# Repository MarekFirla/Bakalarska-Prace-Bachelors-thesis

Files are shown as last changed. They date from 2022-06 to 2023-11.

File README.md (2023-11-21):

# Bakalářská práce
BAKALÁŘSKÁ PRÁCE - KONSTRUKCE LINEÁRNÍCH HODIN

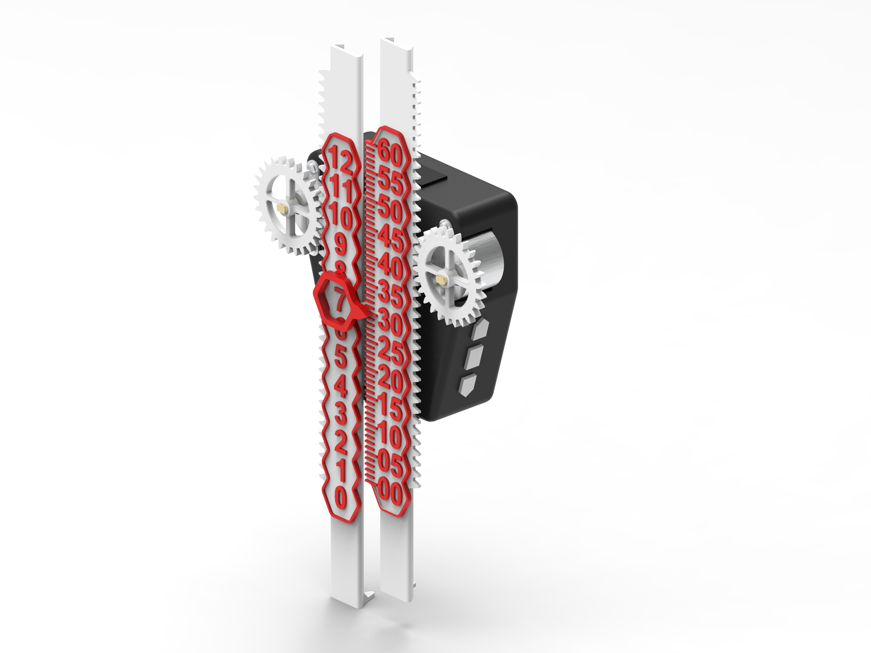
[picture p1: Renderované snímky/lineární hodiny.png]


Zadání bakalářské práce  

Ústav: Ústav konstruování  
Student: Marek Firla  
Studijní program: Strojírenství  
Studijní obor: Základy strojního inženýrství  
Vedoucí práce: doc. Ing. Petr Svoboda, Ph.D.  
Akademický rok: 2020/21  

Ředitel ústavu Vám v souladu se zákonem č.111/1998 o vysokých školách a se Studijním a zkušebním řádem VUT v Brně určuje následující téma bakalářské práce:  

Konstrukce lineárních hodin  
Stručná charakteristika problematiky úkolu:  
Zpravidla existují dvě široce využívaná rozhraní pro měření času. Na jedné straně analogové, které
k zobrazení času využívají rotující ručičky s číselníkem. Na druhé straně digitální s přímým výstupem
ukazatele času pomocí alfanumerických znaků na displeji. Za předpokladu, že čas plyne lineárně, je
však výzvou konstrukce lineárních hodin, které dokážou unikátní cestou zobrazit aktuální čas.

Typ práce: vývojová – konstrukční  

Cíle bakalářské práce:  
Hlavním cílem je konstrukce a následná realizace funkčního vzorku lineárních hodin užitím
technologie 3D tisku a řízené pomocí Arduino Uno s těmito parametry: stupnice s rozsahem 12 hodin
a rozlišitelností 5 minut.  

Dílčí cíle bakalářské práce:
– popsat současné konstrukce lineárních hodin,  
– definovat vhodné parametry pro konstrukční řešení,  
– navrhnout varianty konstrukčních uspořádání,  
– zpracovat výkresovou dokumentaci vybrané varianty včetně řídicího softwaru,  
– realizovat funkční vzorek pomocí 3D tisku.  

ABSTRAKT  
Cílem této práce je popsat návrh, konstrukci a výrobu lineárních hodin. V první části jsou popsány nynější řešení lineárních hodin. Druhá část popisuje návrh a výrobu prototypu lineárních hodin. Hodiny řídí mikrokontrolérová jednotka Arduino UNO, samotné měření času zprostředkovává modul reálného času a pohyb ukazatelů času zprostředkovává dvojice krokových motorů. Realizace je provedena pomocí 3D tisku.   

KLÍČOVÁ SLOVA   

Lineární hodiny, Arduino, 3D tisk  

ABSTRACT  
The main goal of this thesis is to describe the design, construction, and manufacture of linear clocks. The first part describes the current linear clocks design. The second part describes the design of a linear clock prototype. The linear clock is controlled by an Arduino UNO microcontroller unit, the time is measured by the real-time module, the movement of the time indicators is mediated by a pair of stepper motors. Manufacture is done using 3D printing.  

KEYWORDS  

Linear clock, Arduino, 3D print

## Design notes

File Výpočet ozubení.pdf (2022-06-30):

## PŘÍLOHA VÝPOČTY

## 1.1 Základní rozměry

Určení rozměrů základního profilu čelních ozubených kol s evolventním ozubením. Základní definice pojmů je uvedena v normě ČSN 01 4602. Význam jednotlivých pojmů lze

vidět na Obr. 1.

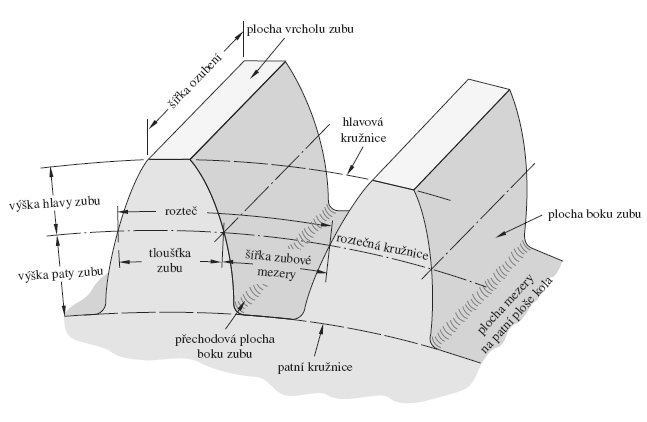
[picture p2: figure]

Obr. 1 Názvosloví čelního ozubeného [33]

### 1.1.1 Vstupní zvolené hodnoty:

Modul volen z tabulky normalizovaných modulů podle ČSN 01 4608:

mn = 1,5 mm

Úhel záběru volen podle ČSN 01 4607:

α = 20°

Jedná se o nekorigované ozubení, jednotkové posunutí je nulové:

x1 = 0

Úhel sklonu zubu je u přímého ozubení nulové:

β = 0°

Minimální počet zubů pastorku, který je v záběru s ozubeným hřebenem, aby nedocházelo k interferenci se určí z následující rovnice: [33], str. 729

zmin =

2 ∙ ℎa

∗
sin² α

=

2 ∙ 1
sin²(20°)

= 17,1 = 17̇

Zvolený počet zubů pastorku:

z1 = 26

Zvolená účinná šířka ozubení:

bw = 1,5 mm

### 1.1.2 Rozměry základního profilu ozubení

Rovnice pro výpočet rozměru ozubeného převodu převzato z [33], tab. 13-1 str. 741 (výběr z normy ČSN 01 4607).

Výška hlavy zubu:

ℎa = mn = 1,5 mm

Výška paty zubu:

ℎf = 1,25 ∙ mn = 1,25 ∙ 1,5 = 1,875 mm

Výška zubu:

ℎ = ℎa + ℎf = 1,5 + 1,875 = 3,375 mm

Hlavová vůle:

cn = 0,25 ∙ mn = 0,25 ∙ 1,5 = 0,375 mm

Rozteč:

pn = π ∙ mn = π ∙ 1,5 = 4,712 mm

Tloušťka zubu na roztečné kružnici:

sn = 0,5 ∙ pn = 0,5 ∙ 4,712 = 2,356 mm

Šířka zubové mezery:

en = sn = 2,356 mm

Poloměr zaoblení přechodové křivky:

pf = 0,38 ∙ mn = 0,38 ∙ 1,5 = 0,57 mm

Základní rozteč:

pb = pn ∙ cos(α) = 4,712 ∙ cos(20°) = 4,428 mm

### 1.1.3 Rozměry pastorku

Výpočet rozměrů přímých čelních ozubených kol [33], str. 722

Roztečná kružnice pastorku:

d1 = z1 ∙ mn = 26 ∙ 1,5 = 39 mm

Hlavová kružnice pastorku:

da1 = d1 + 2 ∙ ℎa = 39 + 2 ∙ 1,5 = 42 mm

Patní kružnice pastorku:

df1 = d1 − 2 ∙ ℎf = 39 − 2 ∙ 1,875 = 35,25 mm

Základní kružnice pastorku:

db1 = d1 ∙ cos(α) = 39 ∙ cos(20°) = 36,648 mm

Průměr valivé kružnice pastorku:

dw1 = d1 = 39 mm

### 1.1.4 Rozměry kola nahrazující hřeben

Pro pevnostní výpočty se ozubený hřeben nahradí ozubeným kolem o vysokém počtu zubů (1000 zubů) [22]

z2 = 1000

Roztečná kružnice kola:

d2 = z2 ∙ mn = 1000 ∙ 1,5 = 1 500 mm

Hlavová kružnice kola:

da2 = d2 + 2 ∙ ℎa = 1500 + 2 ∙ 1,5 = 1 503 mm

Patní kružnice kola:

df2 = d2 − 2 ∙ ℎf = 1500 − 2 ∙ 1,875 = 1 496,25 mm

Základní kružnice kola:

db2 = d2 ∙ cos(α) = 1500 ∙ cos(20°) = 1 409,54 mm

Průměr valivé kružnice kola:

dw2 = d2 = 1 500 mm

### 1.1.5 Součinitel záběru

Osová vzdálenost:

aw =

(z1+z2

)∙mn
2

=

(26+1000)∙1,5
2

= 769,50 mm

Součinitel záběru profilu v čelní rovině pro vnější ozubení [33], str. 727:

εα =

√da1
2 −db1

2 +√da2
2 −db2

2 −2∙aw∙sin(α)

2∙pb

=

√42²−36,648²+√1503²−1 409,54²−2∙769,50∙sin (20°)

2∙4,428

= 1,793

Součinitel záběru kroku:

εβ = 0

Celkový součinitel záběru:

εγ = εα + εβ = 1,793 + 0 = 1,793

## 1.2 Pevnostní výpočet

### 1.2.1 Zatížení

Určení zatížení ozubeného soukolí [33], str. 751

Jmenovitý kroutící moment krokového motoru určený z [15]:

M = 34,4 N ∙ mm

Obvodová síla kola:

Ft =

2M
d1

= 1,759 N

Radiální síla kola:

Fr = Ft

- tan(α) = 0,64 N

Normálná síla kola:

Fn =

Ft
cos (α)

= 1,872 N

### 1.2.2 Materiálové charakteristiky

Mez únavy v ohybu [25]:

σFP = 4,9 MPa

### 1.2.3 Kontrola na ohyb v patě zubu

Výpočet ohybového napětí v patě zubu bude vypočten dle ČSN 01 4686. Výpočet je

zjednodušený a platí pro čelní ozubená kola s přímým a šikmým ozubením. Výpočet se omezuje na ohybové namáhání v patě zubu. [24]

Součinitel tvaru zubu se odečte z přiloženého grafu viz Obr. 2 [24]

YF = 2,6

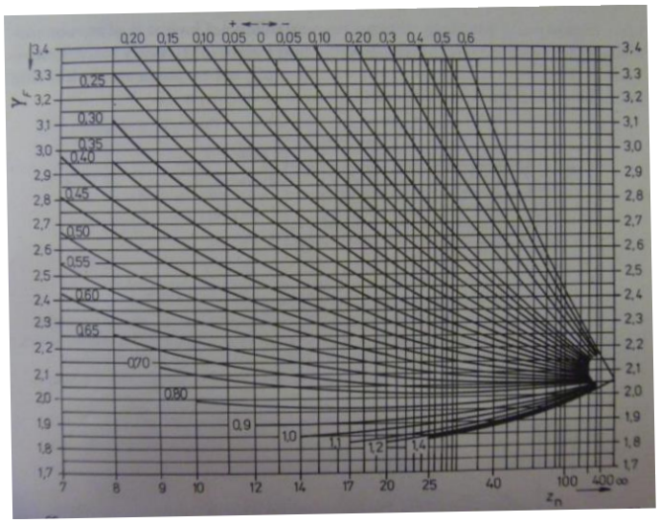
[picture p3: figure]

Obr. 2 Graf součinitele tvaru zubu [24]

Součinitel vlivu trvání záběru evolventy se spočítá z následující rovnice: [24]

Yε =

1
εα

=

1
1,793

= 0,558

Součinitel sklonu zubu se rovná pro přímé ozubení jedné:

Yβ = 1

Ohybové napětí v patě zubu: [24]

σF =

Ft
mn∙bw
- YF ∙ Yε
- Yβ =

1,759
1,5∙1,5
- 2,6 ∙ 0,558 ∙ 1 = 1,133 MPa

Bezpečnost:

SF =

σFP
σF

= 4,324

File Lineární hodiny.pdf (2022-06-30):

# VYSOKÉ UENÍ TECHNICKÉ V BRN

BRNO UNIVERSITY OF TECHNOLOGY

## FAKULTA STROJNÍHO INENÝRSTVÍ

FACULTY OF MECHANICAL ENGINEERING

## ÚSTAV KONSTRUOVÁNÍ

INSTITUTE OF MACHINE AND INDUSTRIAL DESIGN

# KONSTRUKCE LINEÁRNÍCH HODIN

DESIGN OF LINEAR CLOCK

### BAKALÁSKÁ PRÁCE

BACHELOR'S THESIS

### AUTOR PRÁCE

AUTHOR

### Marek Firla

### VEDOUCÍ PRÁCE

SUPERVISOR

doc. Ing. Petr Svoboda, Ph.D.

### BRNO 2021

Fakulta strojního inenýrství, Vysoké uení technické v Brn / Technická 2896/2 / 616 69 / Brno

# Zadání bakaláské práce

Ústav: | Ústav konstruování
Student: | Marek Firla
Studijní program: | Strojírenství
Studijní obor: | Základy strojního inenýrství
Vedoucí práce: | doc. Ing. Petr Svoboda, Ph.D.
Akademický rok: | 2020/21

editel ústavu Vám v souladu se zákonem .111/1998 o vysokých kolách a se Studijním a zkuebním ádem VUT v Brn uruje následující téma bakaláské práce:

## Konstrukce lineárních hodin

Struná charakteristika problematiky úkolu:
Zpravidla existují dv iroce vyuívaná rozhraní pro mení asu. Na jedné stran analogové, které k zobrazení asu vyuívají rotující ruiky s íselníkem. Na druhé stran digitální s pímým výstupem ukazatele asu pomocí alfanumerických znak na displeji. Za pedpokladu, e as plyne lineárn, je vak výzvou konstrukce lineárních hodin, které dokáou unikátní cestou zobrazit aktuální as.

Typ práce: vývojová konstrukní

Cíle bakaláské práce:
Hlavním cílem je konstrukce a následná realizace funkního vzorku lineárních hodin uitím technologie 3D tisku a ízené pomocí Arduino Uno s tmito parametry: stupnice s rozsahem 12 hodin a rozliitelností 5 minut.
Dílí cíle bakaláské práce:
popsat souasné konstrukce lineárních hodin,
definovat vhodné parametry pro konstrukní eení,
navrhnout varianty konstrukních uspoádání,
zpracovat výkresovou dokumentaci vybrané varianty vetn ídicího softwaru,
realizovat funkní vzorek pomocí 3D tisku.

Poadované výstupy: prvodní zpráva, výkresy souástí, výkres sestavení, digitální data. Rozsah práce: cca 27 000 znak (15 20 stran textu bez obrázk).
asový plán, struktura práce a ablona prvodní zprávy jsou závazné: http://ustavkonstruovani.cz/texty/bakalarskestudiumukonceni/

Fakulta strojního inenýrství, Vysoké uení technické v Brn / Technická 2896/2 / 616 69 / Brno

Seznam doporuené literatury:

BROWN, H. T. 507 Mechanical Movements: Mechanisms and Devices. 18th Edition. Wexford College Press, 2010. ISBN 978-1-60386-311-7.

MOLINE, D. J. WAGNER a E. VOLK. Model of a mechanical clock escapement. American Journal of Physics. 2012, 80(7), 599-606. DOI: 10.1119/1.4705517. ISSN 0002-9505.

MAJOR, F. G. Celestial and Mechanical Clocks. The Quantum Beat. New York, NY: Springer New York, 1998, 1-21. DOI: 10.1007/978-1-4757-2923-8_1. ISBN 978-1-4757-2925-2.

RAWLINGS, A. L. The Science of Clocks and Watches. 3rd. Upton, England: British Horological Society, 1993. ISBN 978-0-95096-213-9.

Termín odevzdání bakaláské práce je stanoven asovým plánem akademického roku 2020/21

V Brn, dne

L. S.

prof. Ing. Martin Hartl, Ph.D. editel ústavu

doc. Ing. Jaroslav Katolický, Ph.D. dkan fakulty

## ABSTRAKT

Cílem této práce je popsat návrh, konstrukci a výrobu lineárních hodin. V první části jsou popsány nynější řešení lineárních hodin. Druhá část popisuje návrh a výrobu prototypu lineárních hodin. Hodiny řídí mikrokontrolérová jednotka Arduino UNO, samotné měření času zprostředkovává modul reálného času a pohyb ukazatelů času zprostředkovává dvojice krokových motorů. Realizace je provedena pomocí 3D tisku.

## KLÍČOVÁ SLOVA

Lineární hodiny, Arduino, 3D tisk

## ABSTRACT

The main goal of this thesis is to describe the design, construction, and manufacture of linear clocks. The first part describes the current linear clocks design. The second part describes the design of a linear clock prototype. The linear clock is controlled by an Arduino UNO microcontroller unit, the time is measured by the real-time module, the movement of the time indicators is mediated by a pair of stepper motors. Manufacture is done using 3D printing.

## EYWORDS

Linear clock, Arduino, 3D print

## BIBLIOGRAFICKÁ CITACE

FIRLA, Marek. Konstrukce lineárních hodin. Brno, 2018, 99 s. Vysoké učení technické v Brně, Fakulta strojního inženýrství, Ústav konstruování. Vedoucí diplomové práce

doc. Ing. Petr Svoboda, Ph.D.

## PODĚKOVÁNÍ

Na tomto místě bych rád poděkoval doc. Ing. Petru Svobodovi, Ph.D. za odborné vedení mé práce.

## PROHLÁŠENÍ AUTORA O PŮVODNOSTI PRÁCE

Prohlašuji, že diplomovou práci jsem vypracoval samostatně, pod odborným vedením doc. Ing. Petra Svobody, Ph.D. Současně prohlašuji, že všechny zdroje obrazových a textových informací, ze kterých jsem čerpal, jsou řádně citovány v seznamu použitých zdrojů.

Podpis autora

## OBSAH

1 | ÚVOD | 13
2 | PŘEHLED SOUČASNÉHO STAVU POZNÁNÍ | 14
2.1 | Čas | 14
2.2 | Lineární hodiny | 14
| CLOQ The linear clock. | 16
| Linear Clockworks | 16
| Linear clock by JanDerogee | 17
| Linear clock by Euphy | 18
| Linear clock by Audun Ask Blaker | 18
2.3 | Arduino | 19
| Arduino IDE | 19
| Arduino UNO | 20
| Arduino klony | 20
| Arduino Shieldy | 20
3 | ANALÝZA PROBLÉMU A CÍL PRÁCE | 21
3.1 | Analýza problému | 21
3.2 | Cíl práce | 21
4 | KONCEPČNÍ ŘEŠENÍ | 22
4.1 | Komponenty | 22
| Řízení Hodin | 22
| Motory | 23
| Řízení motorů | 24
| Měření času | 24
| Ovládací rozhraní | 25
| Polohování | 25
4.2 | Koncepční uspořádání č. 1 | 26
4.3 | Koncepční uspořádání č. 2 | 27
4.4 | Koncepční uspořádání č. 3 | 27
5 | KONSTRUKČNÍ ŘEŠENÍ | 28
5.1 | Zapojení | 28
5.2 | Konstrukční rozvržení | 29

5.3 | Návrh krytů | 30
| Upevnění modulů | 30
5.4 | Převodový mechanismus | 32
| Převod ozubeným hřebenem | 32
| Vedení | 34
5.5 | Návrh ciferníků a indikátoru | 36
5.6 | Výroba | 36
| Materiál | 37
| Nastavení tisku | 37
5.7 | Sestavení programu | 38
| Načtení knihoven a deklarace proměnných | 39
| Nastavení zařízení | 40
| Hlavní struktura programu | 41
| Synchronizace | 42
| Nastavení výchozí polohy | 42
| Nastavení hodin | 43
| Alarm | 44
| Ošetření zákmitů tlačítek | 45
| Spotřeba energie | 45
5.8 | Sestavení lineárních hodin | 45
5.9 | Náklady | 47
6 | DISKUZE | 49
7 | ZÁVĚR | 50
8 | SEZNAM POUŽITÝCH ZDROJŮ | 51
9 | SEZNAM POUŽITÝCH ZKRATEK, SYMBOLŮ A VELIČIN | 54
10 | SEZNAM TABULEK | 56
11 | SEZNAM OBRÁZKŮ A GRAFŮ | 57
12 | SEZNAM PŘÍLOH | 58

## 1 ÚVOD

Čas je pro celé lidstvo klíčovým faktorem už od jeho počátku. Tento fakt přinesl vytvoření

nejen časových systémů, ale taktéž vývoj časomír. Vývoj probíhal nejen z hlediska stále přesnějšího měření času, ale také se měnily způsoby jeho zobrazení. Pokud se na současné časomíry podíváme v souvislosti s rozhraním pro zobrazovaní času tak narazíme na dvě nejvíce rozšířené varianty. První je analogové rozhraní zahrnující pevný ciferník a dvě nebo tři pohyblivé ručičky pro hodiny a minuty, popřípadě i sekundy. Druhou možností je zobrazení času skrze znaky na alfanumerickém displeji. Méně tradiční způsob zobrazení času nám poskytují lineární hodiny. Právě proto je poskytnutí rešerše dosavadních znalostí a návrh lineárních hodin cílem této bakalářské práce.

Jelikož trh s tímto řešením zobrazení času není příliš rozsáhlý, bylo nasnadě vytvořit nový konstrukčně jednoduchý funkční model levných lineárních hodin realizovaný pomocí 3D tisku a řízený skrze mikrokontrolérovou jednotku Arduino.

## 2 PŘEHLED SOUČASNÉHO STAVU POZNÁNÍ

## 2.1 Čas

Čas je základní fyzikální veličina soustavy SI s označením t. Může být definována jako:

Neprostorové kontinuum, ve kterém se události odehrávají ve zjevně nevratném pořadí od minulosti přes přítomnost až do budoucnosti. [1] Základní jednotkou je sekunda. Sekunda, značka „s“, je jednotka času v SI. Je definována fixací číselné hodnoty cesiové frekvence ΔνCs, tedy frekvence přechodu mezi hladinami velmi jemného rozštěpení neporušeného základního stavu atomu cesia 133, aby byla rovna 9 192 631 770, je-li vyjádřena jednotkou Hz, rovnou s−1. [2]

Hodiny (časomíry) jsou přístroje určené k přímému měření času. Měření času v nich probíhá z pravidla dvojím způsobem. Buď přímým sledováním rovnoměrného pohybu anebo počítáním pravidelných pohybů mechanických, elektrických nebo atomárních oscilací. [3] První způsob měření času je typický pro sluneční, přesýpací nebo vodní hodiny. Druhý způsob měření času je častější. Jedná o hodiny mechanické, kde se sleduje pohyb kyvadla, elektronické, využívající piezoelektrického jevu, nebo atomové kde se sleduje rezonanční frekvence atomu nejčastěji celsia.

## 2.2 Lineární hodiny

Lineární hodiny je časomíra s jedinečným způsobem zobrazení času, jejímž charakteristickým znakem je nahrazení tradičního kulatého ciferníku nebo alfanumerického displeje, ciferníkem přímým. Ručičky, ciferníky nebo jiné indikátory se pohybují po lineární, křivočaré, lomené nebo smíšené trajektorii a na následně se vracejí do výchozí polohy. [4] Jinými slovy indikátory se pohybují po neuzavřené křivce vratným pohybem.

Jeden z prvních konceptů lineárních hodin byl vytvořen kolem roku 1941. Nicméně původní zařízení sloužilo pouze pro zobrazování času jako dodatek ke standartnímu mechanickému hodinovému strojku. [4] Zařízení se připojovalo na příslušnou hodinovou minutovou nebo i sekundovou výstupní hřídel hodin.

Samotné zařízení se skládá z ciferníku ve tvaru lišty (viz Obr. 2-1 Koncepční náčrt řešení lineárních hodin) s čísly symbolizující hodiny. Na obou koncích ciferníku se nachází dvojice kladek (G, G´) na kterých je navinuto lanko (X), na němž je pevně ukotven indikátor času (R). Indikátor času (R) je uložen v lineárním vedení (V). První z kladek (G) je spojena s výstupní hřídelí hodinového strojku pomocí spojky. Spojka se skládá ze čtyř součástí: páky (CDE), drápu (A), tažné pružiny (J) a dorazu (K). Chodem hodinového strojku se otáčí i kladka (G) na kterou se navíjí lanko (X) a pohybuje se i indikátor (R) po ciferníku. Druhá kladka (G´) ze které se lanko (X) odvíjí, je spojena se spirálovou pružinou (P´). Otáčením kladky (G´), v důsledku odvíjení lana (X), se spirálová pružina (P´) stlačuje a vytváří kroutící moment (S´´), který působí proti pohybu. Jednou za celou otáčku kladky (G) se spojka (páka CDE a „dráp“ A) rozepne a rozpojí hodinový strojek od kladky (G), čímž se kladka (G) začne volně otáčet. Stlačená pružina (P´) poté začne otáčet kladkou (G´) a navíjet lanko (X), čímž se posune indikátor času (R) zpět do výchozí polohy. [4]

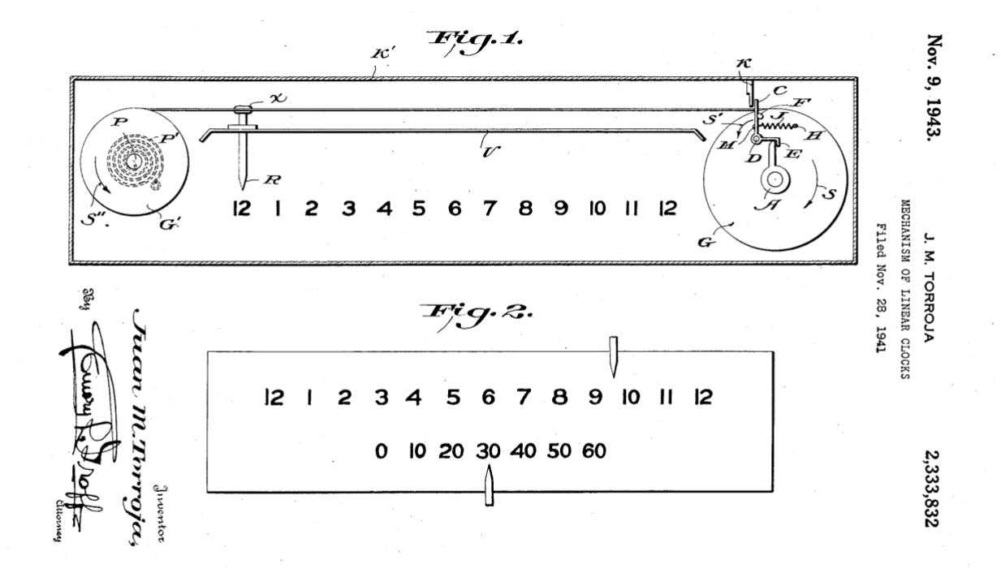
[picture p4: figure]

Obr. 2-1 Koncepční náčrt řešení lineárních hodin [4]

V současnosti se výrobou a prodejem tohoto netradičního způsobu zobrazování času zabývá jen velmi málo firem. Díky tomu mnoho návrhů na konstrukci pochází z dílny amatérů a hobby tvůrců. Projekty, z nichž jsem čerpal inspiraci pro vytvoření vlastního modelu, představím v následujících kapitolách.

CLOQ The linear clock.

Se zajímavým řešení lineárních hodin přišel britský designer Rob Lafratta (http://roblafratta.com/) v roce 2015. Jeho koncept lineárních hodin se inspiruje starými analogovými rádii a experimentuje s myšlenkou o zobrazení času v jedné linii. Jeho vize byla zjednodušit design standartních hodin s kruhovým ciferníkem a přinést zajímavé řešení zobrazení času. [5]

Samotné hodiny ovšem na rozdíl od původního konceptu neobsahují pohyblivé součásti a zobrazování hodin zde probíhá pomocí LED podsvícení. Každé z čísel na liště zde představuje příslušnou hodinu a podsvícením určitého čísla se určí aktuální hodina. Minuty jsou reprezentovány tečkami pod číslicemi hodin. Počet rozsvícených teček pak představuje pětiminutový časový interval.

Design hodiny si můžeme prohlédnout na přiloženém obrázku (viz Obr. 2-2)

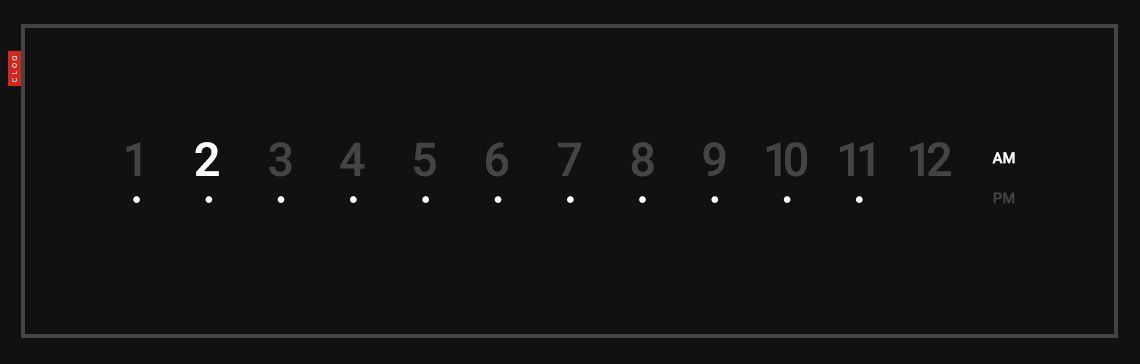
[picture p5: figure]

Obr. 2-2 Design CLOQ lineárních hodin [5]

### Linear Clockworks

Další řešení lineárních hodin přináší konstruktér Lindsay Morris a jeho firma Linear Clockworks (USA – Asheville), která vyrábí lineární hodiny na zakázku.

Samotné lineární hodiny se skládají z ciferníku, který je v podobě dlouhé lišty s čísly od 6 do 12 (viz obr. 2-3). Po tomto ciferníku se během dne směrem doprava pohybuje pouze jeden ukazatel, který určuje aktuální čas s rozlišitelností 15 minut. O půlnoci se pohyb reverzuje a ukazatel se začne pohybovat zpět doleva, přičemž návrat do výchozí polohy na 6:00 trvá šest hodin. Samotný ukazatel je pevně spojený s krytem pro elektroniku, která se pohybuje společně s ukazatelem. Řídící jednotka se skládá z řídícího obvodu, obvodu reálného času

(RTC obvod), displeje pro pohodlnější nastavení času a dvou tlačítek. Samotný pohyb potom zajišťuje připojený krokový motor. Hodiny jsou napájeny baterií, která vydrží 9 až 12 měsíců a dobíjí se pomocí USB konektoru. Firma vyrobené lineární hodiny prodává od 250 od 925 dolarů v závislosti na zvoleném designu. [6]

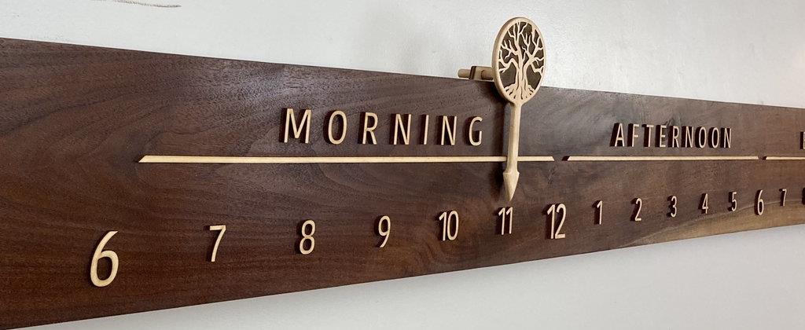
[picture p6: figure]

Obr. 2- 3 Jeden z designů nabízející firma Linear Clockworks [6]

### Linear clock by JanDerogee

Tyto lineární hodiny se inspirují designem starých mechanických hodin a uveřejnil je Jan Derogee na svých osobních webových stánkách.

Ciferník je rozdělen do dvou sloupců, ve kterých jsou napsány číslice symbolizující hodiny (viz obr. 2-4). Levý sloupec symbolizuje dopolední hodiny, pravý odpolední. Mezi sloupci se ve středu ciferníku nachází závitová tyč, na které se nachází jediná ručička. Samotná ručička je pak opřena o vodivou „senzorovou tyč“, umístěnou na vnějších stranách ciferníku, která slouží jako opora ručičky a taktéž se na ni nastavuje čas alarmu. V případě, že se závitová tyč otáčí, dochází k zvedání nebo spouštění ručičky, která určuje aktuální čas. Tato závitová tyč je pevně spojena s výstupní hřídelí krokového motoru. Motor se nachází ve spodní časti hodin společně s řídící elektronikou. Hodiny řídí mikročip ESP8266. Požitý krokový motor má označení 28BYJ-48. Na hodinách se taktéž nachází dvojice reproduktorů pro zvukovou signalizaci alarmu. [7]

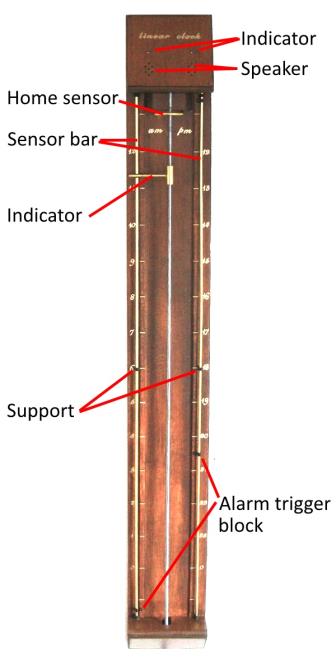
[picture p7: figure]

Obr. 2-4 Design lineárních hodin [7]

### Linear clock by Euphy

Tento projekt opět přinesl trochu odlišný přístup k řešení lineárních hodin, který více reflektuje původní koncept.

Základem je opět dlouhý ciferním ve tvaru lišty s čísly hodin a minut. Přímo na jednom z konců ciferníku jsou připevněny krokové motory a řídící elektronika jejichž hlavním kontrolérem je deska Arduino UNO. Na každé z výstupních hřídelí krokových motorů se nachází dva páry kladek. Další samostatná pomocná kladka je umístěna na opačném konci ciferníku. Na jednu z kladek na hřídeli motoru je namotáno lanko, které je následně přetaženo přes pomocnou kladku a upevněno k druhé kladce na hřídeli motoru. [8] Otáčením se převíjí lanko z jedné kladky na hřídeli motoru přes pomocnou kladku na kladku druhou. Na lanku je poté umístěn indikátor, který se přesouvá společně s ním po ciferníku čímž se zobrazuje čas.

### Linear clock by Audun Ask Blaker

Tyto lineární hodiny vytvořil průmyslový designér Audun Ask Blaker. (https://askblaker.com/)

Čas je zde vytištěn na uzavřeném pásmě, které je navinuto mezi rotujícími válci (viz Obr. 2-

5 b). Jeden z válců je poté pomocí ozubeného převodu řízen skrze elektromotor. Otáčením elektromotoru dojde k rotaci jednoho z válců a pásmo se začne převíjet mezi válci. Pohyb pásma vůči indikátoru, který je pevně spojen s konstrukcí hodin, poté způsobuje zobrazování času. [9]

Samotný design si můžete prohlédnout na přiloženém obrázku (viz Obr. 2-5 a)

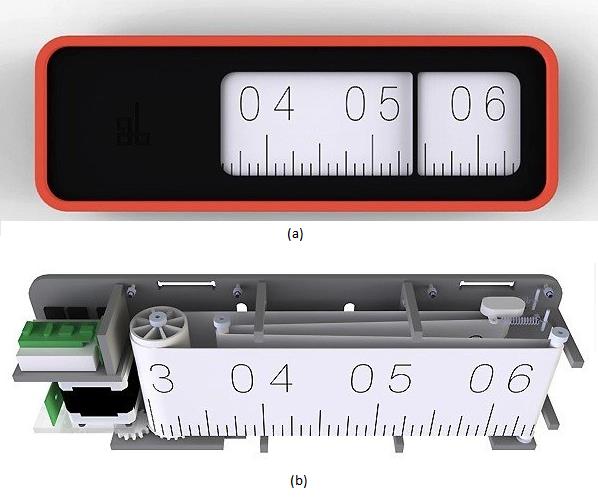
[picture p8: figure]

Obr. 2-5 Design lineárních hodin by Audun Ask Blaker (a) design hodin (b) vnitřní mechanismus [9]

## 2.3 Arduino

Arduino je open source elektronická platforma založena na mikrokontrolerech ATmega od firmy Atmel. Jedná se o jednoduchý programovatelný jednodeskový počítač, který vytvořil Massimoha Banzi v roce 2005. Původním cílem projektu Arduino bylo vytvoření levného intuitivního vývojového setu, který pomůže ve výuce studentů na školách, avšak projekt byl natolik úspěšný že se rozšířil i mezi veřejnost do celého světa. 51[10] Díky této skutečnosti vznikla kolem této platformy velká komunita, která sdílí mezi sebou poměrně velké množství návodů a projektů.

### Arduino IDE

V rámci platformy Arduina vzniklo kromě samotných vývojových desek i vlastní vývojové prostředí s názvem Arduino IDE (integrated development environment = integrované vývojové prostředí). Vývojové prostředí Arduino IDE je napsáno v jazyce Java a vychází z jiného výukového prostředí s názvem Processing, které bylo upraveno přidáním mnoha funkcí a podpory knihovny Wiring. Samotné Arduino je možné programovat v programovacím jazyce C nebo C++, nejjednodušší programování je právě za pomocí knihovny Wiring. [10] Vzhledem k tomu je právě knihovna Wiring pro programování Arduina v současnosti velmi oblíbená a rozšířená.

Samotnou strukturu programu lze rozdělit do několika bloků (viz Obr. 2-6). Prvním z nich je blok (funkce) void setup(). V tomhle bloku se nachází kód, který se provede na začátku programu pouze jednou. To znamená, buď po nahrání kódu, připojení napájení nebo stisknutí tlačítka pro restart. Dalším z bloků je (funkce) void loop(). Jedná se o nekonečnou smyčku. Příkazy vepsané do této smyčky se neustále opakují až do vypnutí napájení. Dalším blokem jsou řádky ještě před funkcí void setup(). Zde se inicializují knihovny a mohou se zde deklarovat proměnné použité v programu. [10]

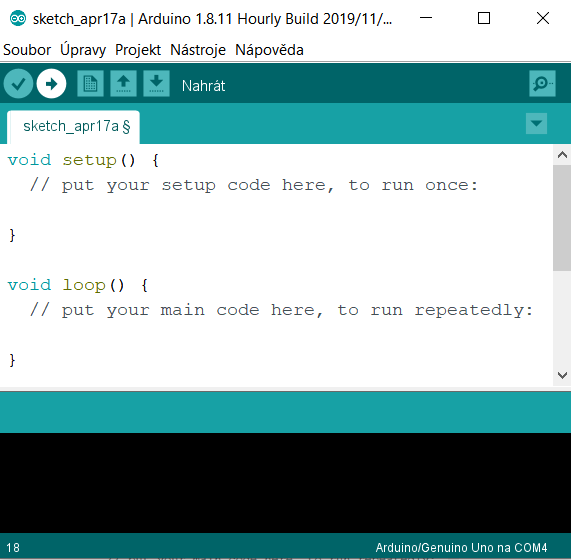
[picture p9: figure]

Obr. 2-6 Prostředí Arduino IDE [10]

### Arduino UNO

Arduino Uno (viz Obr. 2-7) je jednou z nejpoužívanějších desek jakou platforma Arduino nabízí a je přímým pokračovatelem hlavní vývojové linie. Aktuálně je v prodeji třetí verze této desky. Na desce se nachází procesor ATmega328, USB port i s převodníkem pro snadné a pohodlné připojení k počítači pro nahrání programu a napájecí souosý konektor pro snadné napájení desky. Na desce se nachází 14 digitálních pinů nastavitelných jako vstupní i výstupní a 6 analogových vstupních pinů. [10]

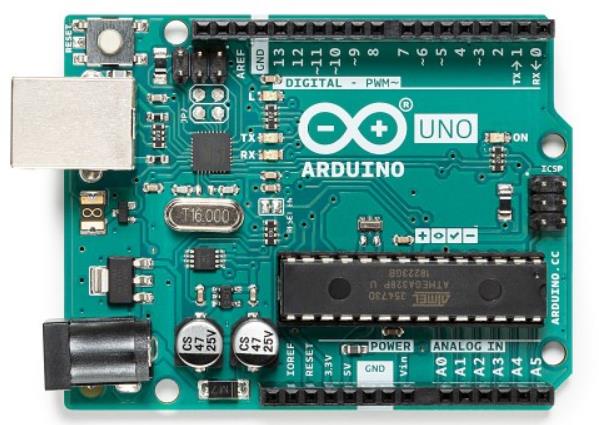
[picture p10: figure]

Obr. 2-7 Arduino UNO REV3 51[11]

### Arduino klony

Vzhledem k open source povaze platformy Arduino tak mimo oficiální řadu vzniklo i mnoho desek neoficiálních, takzvané klony. Setkat se můžeme s klony, které jsou tvarově a výbavou téměř totožné s oficiálními modely a liší se například jen cenou. Nicméně se můžeme setkat i s klony, které jsou přizpůsobené jen k jedné konkrétní činnosti. [10]

### Arduino Shieldy

Výhodou platformy Arduino je možnost rozšířit jeho funkce pomocí tzv. shieldů. Jedná se o elektronickou desku připojitelnou na desku Arduino pomocí pinů, které se nasunou do příslušných zdířek. [10] Výhodou je jednoduchost propojení s deskou Arduino bez nutnosti použít propojovací vodiče. Obdobně jako je mnoho typů Arduino desek, tak také existuje i celá řada shieldů například Ethernet Shield, Wifi Shield, Motor Shield a další. Při výběru je však nutné dávat si pozor na kompatibilitu shieldu s deskou Arduino. [10]

## 3 ANALÝZA PROBLÉMU A CÍL PRÁCE

## 3.1 Analýza problému

Na základě analýzy současných řešení můžeme rozlišit dva typy lineárních hodin. Prvním typem jsou hodiny bez pohyblivých častí, kde se aktuální čas zobrazuje nejčastěji pomocí světelné signalizace. Druhý typ poté využívá pohyby indikátoru (ručička) vůči ciferníku nebo pohyb ciferníku vůči indikátoru. Pokud se podíváme na lineární hodiny z hlediska jejich zamýšleného umístění zjistíme, že většina projektů tvoří rozměrově větší časomíry určené k zavěšení na zeď. Nicméně rozměrově menší lineární hodiny, které by bylo možné umístit například na pracovní stůl, zcela chybí. V práci je tedy řešena právě problematika lineárních hodin s pohyblivými částmi, které by měly dostatečně malé rozměry pro umístění na polici či pracovní stůl.

V rámci práce pak musí být vyřešena problematika měření a vhodného zobrazování času. Parametry, které musíme v návrhu zohlednit jsou především cena jednotlivých komponentů a materiálů, spotřeba energie, tichý chod a nízká hmotnost a rozměry. Navíc mezi základní funkce musí patřit snadné a intuitivní odečítání času z lineárních hodin, automatické seřízení času po znovuobnovení napájení, snadná a pohodlná možnost přenastavení času a v neposlední řadě funkce nastavitelného alarmu.

## 3.2 Cíl práce

Hlavním cílem práce je navrhnou konstrukci a vyrobit funkčního modelu lineárních hodin za pomocí 3D tisku.

Dílčí cíle bakalářské práce:

- Výběr řídícího hardwaru pro zajištění všech funkcí lineárních hodin.
- Výběr mechanismu a celkového konstrukčního uspořádání lineárních hodin
- Návrh krytů a upevnění elektroniky v modelu.
- Návrh mechanismu pro chod hodin.
- Návrh zobrazovacích prvků lineárních hodin.
- Výroba prototypu lineárních hodin pomocí 3D tisku.
- Vytvoření a optimalizace řídícího programu.

## 4 KONCEPČNÍ ŘEŠENÍ

Hlavním cílem této kapitoly je vyřešit dva základní konstrukční uzly, a to rozhodnout o řídících komponentách, které určí základní funkce a parametry lineárních hodin. Následně zvolit vhodné rozvržení hodin a mechanismus pohybu indikátoru.

## 4.1 Komponenty

V následné kapitole bude rozebráno a zdůvodněno zvolení komponent použitých v lineárních hodinách. Jedná se o elektronické obvody zajišťující funkce lineárních hodin jako jsou měření času, pohyby indikátorů a alarm.

### Řízení Hodin

Základem řízení zde bude jednotka Arduina UNO, ke kterému se poté standartně připojí ostatní potřebné moduly k rozšíření funkcí Arduina.

Kromě originální desky Arduino UNO je možné vybírat i ve velkém množství jeho klonů. Pro tuto práci byl vybrán klon Arduino UNO od firmy Eses. Tento klon si zachovává všechny důležitě funkce a základní parametry originální desky a jediným znatelným rozdílem je využití jiného USB převodníku s označením CH340. Důvodem vybrání tohoto klonu na rozdíl od originální desky byla především nižší cena. Základní parametry zvolené desky uvádím v následující tabulce (viz Tab. 4-1). [12]

Základní charakteristika Arduino UNO (klon)

Hlavní čip | ATmega328
Frekvence procesoru | 16 MHz
Velikost Flash paměti | 32 KB
Převodník | USB CH340
Max. vstupní napětí | 6 až 20 V
Počet digitálních I/O pinů | 14
Počet analog. vstup. pinů | 6
Max. proud I/O pinem | 20 mA
Max. proud 3V3 pinem | 50 mA
Rozměry | 68,6 x 53,4 mm
Hmotnost | 25 g
Tab. 4-1 Základní parametry Arduina UNO (klon) [12]

### Motory

Pro správnou funkci lineárních hodin je nutné zvolit vhodný typ motoru, na něž je jako hlavní požadavek kladeno přesné polohování výstupní hřídele. Mezi další požadavky patří nízká cena, malé rozměry a také snadné řízení.

Možným řešením je použití polohového servopohonu. Servopohon je regulační pohon, jenž se sestává z jednoho nebo více elektrických motorů, napájecích výkonových měničů a řídicích a regulačních obvodů . Servopohon je zapojen vždy v uzavřené regulační smyčce, se zpětnou vazbou rychlostní a většinou i polohovou. [13]

Dalším uvažovaným řešením je využití krokového motoru. Krokové motory jsou synchronní stroje. Pohyb zde není spojitý, ale realizuje se pomocí kroků. Krok je přeskok mezi stabilními polohy motoru vždy o úhel daný konstrukcí motoru. [14]

Výhodou krokových motorů vůči servopohonům v této aplikaci je možnost nastavovat polohu krokového motoru bez nutnosti zpětné vazby, což velmi zjednodušuje řízení motoru. Další výhodou je nižší cena oproti servopohonu. Ovšem jejich velikou nevýhodou je znatelný pokles momentu při zvyšujících se otáčkách, kterým servopohony netrpí.

Po zvážení parametrů a kritérií byl nakonec vybrán krokový motor s označením 28BYJ-48. 52[15] Představuje jeden z nejpoužívanějších a nejlevnějších miniaturních krokových motorů na trhu. Jedná se o unipolární krokový motor se jmenovitým napětím 5 V. Další základní charakteristiky jsou uvedeny v přiložené tabulce (viz Tab. 4-2).

Základní charakteristiky krokového motoru 28BYJ-48

Rated voltage (Jmenovité napětí) | 5 VDC
Number of Phase (počet fází) | 4
Speed Variation Ratio (převodový poměr) | 1/64
Step Angle (Velikost kroku) | 11,25°
Steps per revolution (Počet kroků na otáčku) | 2 048
Idle In-traction Frequency (max. rozběhová frekvence) | > 600 Hz
Idle Out-traction Frequency (max. frekvence při chodu) | > 1 000 Hz
In-traction Torque (max. točivý moment) | >34.3 mN.m (120 Hz)
Friction torque (zbytkový moment) | 600-1 200 gf.cm
Pull in torque (rozběhový točivý moment) | 300 gf.cm
Rise in Temperature (Zvýšení teploty) | <40 K(120Hz)
Tab. 4-2 Charakteristiky krokového motoru 28BYJ-48 [15]

### Řízení motorů

Krokový motor však není možné připojit k Arduinu přímo, ale musí být připojen pomocí budiče (driveru). Driver krokového motoru je elektronický obvod, který na základě řídících signálů generuje impulsy v určitém sledu a délce. Tyto impulsy spínají jednotlivá vinutí krokového motoru, což řídí počet kroků a smysl otáčení. [14]

Drivery existují v několika vyráběných konstrukčních variantách. Jednou z nich je použití Arduino shieldu, u kterého je výhoda snadného připojení na příslušnou Arduino desku (viz kapitola 2.3.4). Další možnost je použití samostatného modulu, u kterého je ovšem nutné k propojení s deskou Arduino použít propojovací vodiče. Výhodou tohoto řešení je ovšem zpravidla nižší cena a rozměry než u shieldů.

Vybraný modul Motor driver A3967 byl zvolen zejména na základě nízké ceny, vhodného rozmezí pracovních hodnot napětí a proudu pro zvolený krokový motor. [16] Mezi funkce tohoto driveru pak patří možnost změny pracovního kroku, uspání driveru za účelem snížení spotřeby energie a snadné řízení motorů pomocí dvou pinů. Další výhodou tohoto modulu jsou montážní otvory pro šrouby. Základní charakteristiky jsou uvedeny v následující tabulce (viz Tab. 4-3).

Základní charakteristiky pro Motor driver A3967

Load Supply Voltage Range (rozsah napájecího napětí) | 4,75 – 30 V
Output Current range (maximální výstupní proud) | 150 – 750 mA
Logic Supply Voltage Range (rozsah ovládacího napětí) | 3 – 5,5 V
Operation Temperature Range (operační teplota) | -20 – 85 °C
Rozměry | 48 x 20 mm
Tab. 4-3 Charakteristiky Motor driveru A3967 [16]

### Měření času

Modul reálného času (dále RTC modul) je elektronický obvod sloužící k přesnému měření času. Pro potřeby hodin je tento modul velice vhodný, jelikož vnitřní oscilátor Arduina vykazuje větší chybu v měření času. Dalšími výhodami modulu je vlastní zdroj energie řešený v podobě baterie vloženého do modulu. Toto je výhodné zejména, pokud dojde k výpadku primárního zdroje napětí napájející Arduino, protože v tomto případě RTC modul bude dále čas měřit. Po znovuobnovení primárního zdroje nebude nutné znovu nastavovat manuálně čas na hodinách. Samotná spotřeba energie modulu je poměrně malá a na baterii je schopen tento modul fungovat po dobu několika let.

Vybraný modul s označením RTC Hodiny reálného času DS323 (RTC modul) bude v projektu uchovávat informace o aktuálním čase. Samotný modul komunikuje přes rozhraní I2C. Podporované formáty času jsou: sekundy, minuty, hodiny, dny, měsíce a roky, včetně přestupných let. Modul je schopný čas uchovat díky záložní baterii typu LIR2032. 52[17] Základní charakteristiky jsou uvedeny v následující tabulce (viz Tab. 4-4).

Základní charakteristiky pro RTC modul

Čip | DS3231
Přesnost | ±2ppm (±0,432 sekund/den)
Paměť | AT24C32 IIC EEPROM paměť 32k
Rozměry | 38 x 22 x 14 mm
Tab. 4-4 Charakteristiky RTC modulu [17]

### Ovládací rozhraní

Pro nastavování času na lineárních hodinách je nutné navrhnout příslušné ovládací prvky. U většiny běžně prodávaných hodin se vyskytuje trojice tlačítek pro nastavování času, popřípadě data. V tomto případě byly vybrány trojice mikrospínačů. Krajní spínače (tlačítko UP a tlačítko DOWN) zde budou ke zvyšování nebo k snižování dané veličiny a prostřední spínač (tlačítko SET) k přepínání mezi módy pro nastavení hodin. Samotné mikrospínače budou umístěny na plošném spoji s montážními otvory.

Pro snadné nastavování času je dále přidán i displej. Vyhovující je modul, který minimálně zobrazuje čtyři číslice pro zobrazování hodin a minut. Vybraný modul hodinového displeje je navíc opatřen řadičem TM1637, který zjednodušuje připojení modulu na Arduino i jeho následné programování.

### Polohování

Po zapojení napájení sestrojených lineárních hodin je nutné, aby Arduino dokázalo určit aktuální polohu indikátoru, popřípadě dorazit do výchozí polohy a synchronizovat aktuální čas s časem zobrazeným.

Jeden z možných řešení je zapisovat po každém pohybu indikátoru jeho aktuální polohu do paměti, na které tato informace zůstane zapsaná i po odpojení napájení. Výhodou tohoto řešení je vyhnutí se použití koncových spínačů nebo dalších senzorů. Nevýhodou však je, že toto řešení nepočítá s možným vnějším zásahem, který silou posune indikátor do jiné polohy. Arduino poté nemá žádný způsob, jak tuto chybu korigovat a musí se zadat aktuální hodnota polohy do programu ručně. Další problém nastává v oblasti samotného ukládání hodnoty. Arduino i RTC modul sice obsahují EEPROM paměti, které uchovávají hodnoty i po odpojení napájení, nicméně mají jen omezený počet zapsání, a to přibližně 100 000, což by zapříčinilo snížení životnosti hodin. [18]

Dalším řešením je použití hardwarových koncových spínačů. Po připojení napájení se indikátor začne pohybovat směrem k výchozí poloze. Až indikátor dorazí do zamýšlené výchozí polohy narazí na koncový spínač, který sepne. Po sepnutí se do programu nahrají hodnoty aktuální polohy indikátoru.

Po porovnání řešení bylo rozhodnuto o použití koncových spínačů i přes nutnost použití dalších elektrotechnických součástek u tohoto řešení.

## 4.2 Koncepční uspořádání č. 1

Toto řešení vychází z mechanismu pro převod rotačního na lineární pohyb, a to pomocí pohybového šroubu. Základem řešení je vertikální ciferník připojený k základně (viz Obr. 4-1), ve které se nachází veškerá potřebná řídící elektronika pro měření času a ovládání lineárních hodin a dvojice elektromotorů. K výstupním hřídelím elektromotorů jsou připojeny pohybové šrouby, na kterých jsou umístěny indikátory. Otáčením řízených elektromotorů se zdvihají nebo spouští indikátory čímž se ukazují minuty a hodiny. Přetáčení indikátorů brání přidaná vodící lanka, které prochází otvorem v indikátoru.

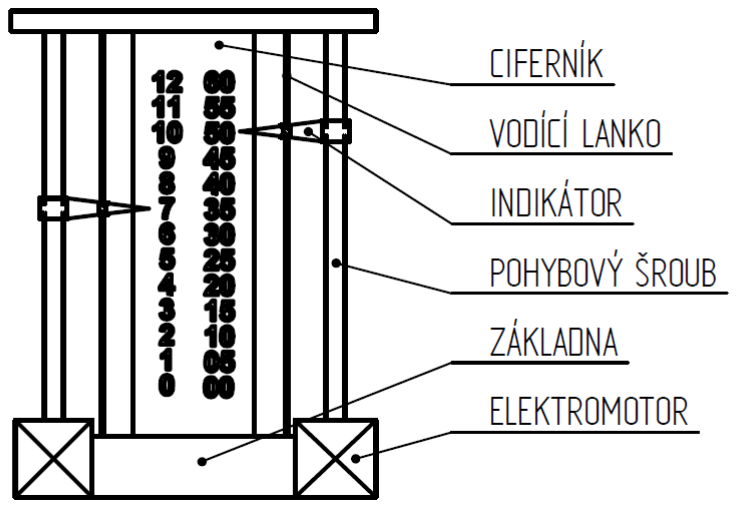
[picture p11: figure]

Obr. 4-1 Schéma konceptu č. 1

## 4.3 Koncepční uspořádání č. 2

U tohoto řešení je použit jako převodový mechanismus ozubený hřeben. Ke krytu obsahující řídící elektroniku je připevněna dvojice elektromotorů. Na výstupních hřídelích elektromotorů jsou připojeny ozubená kola, které zabírají s ozubeným hřebenem. Samotný pár ozubených hřebenů je uložen v lineárním vedení, které jej spojuje s krytem elektroniky. Hodinové a minutové ciferníky jsou poté pevně spojeny s ozubenými hřebeny. Indikátor je pevně spojen s krytem elektroniky. Chodem krokových motorů se otáčí ozubená kola, která spolu zabírají se zuby ozubených hřebenů. Otáčení způsobuje pohyb ozubených hřebenů a s ním spojených ciferníků vůči indikátoru (viz Obr. 4-2).

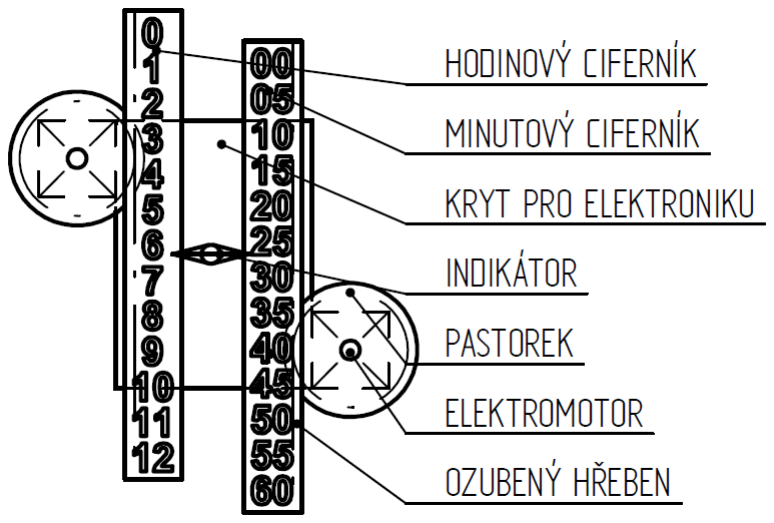
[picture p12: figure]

Obr. 4-2 Schéma konceptu č. 2

## 4.4 Koncepční uspořádání č. 3

Třetí možné řešení využívá jako převod synchronní řemenový převod, na kterém je umístěný indikátor. K samotnému ciferníku je přepojeny dva páry řemenic. Vždy jedna řemenice z páru je pak připojena na výstupní hřídel řízeného elektromotoru. Společně s otáčením motoru se otáčí i řemenice která pohybuje s řemenem a k němu připojený indikátor se pohybuje po ciferníku což zobrazuje čas (viz Obr. 4-3).

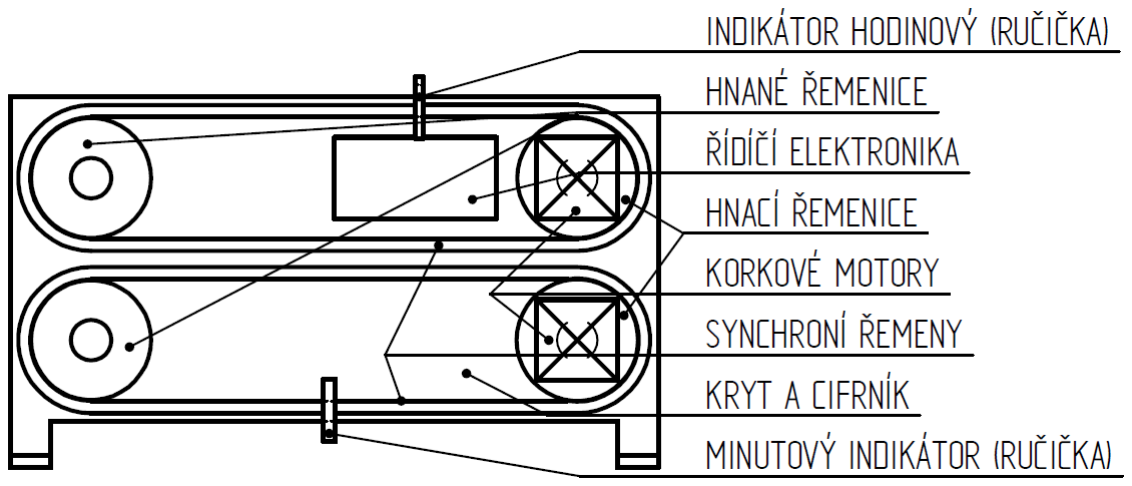
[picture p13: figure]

Obr. 4-3 Schéma konceptu č. 3

## 5 KONSTRUKČNÍ ŘEŠENÍ

Za finální zvolené konstrukční řešení bylo zvoleno koncepční řešení číslo 2 a to zejména z důvodů způsobu výroby modelu pomocí FDM 3D tisku.

## 5.1 Zapojení

Všechny jednotlivé komponenty byly zapojeny k řídící desce Arduino UNO podle přiloženého elektrického schématu (viz Obr. 5-1).

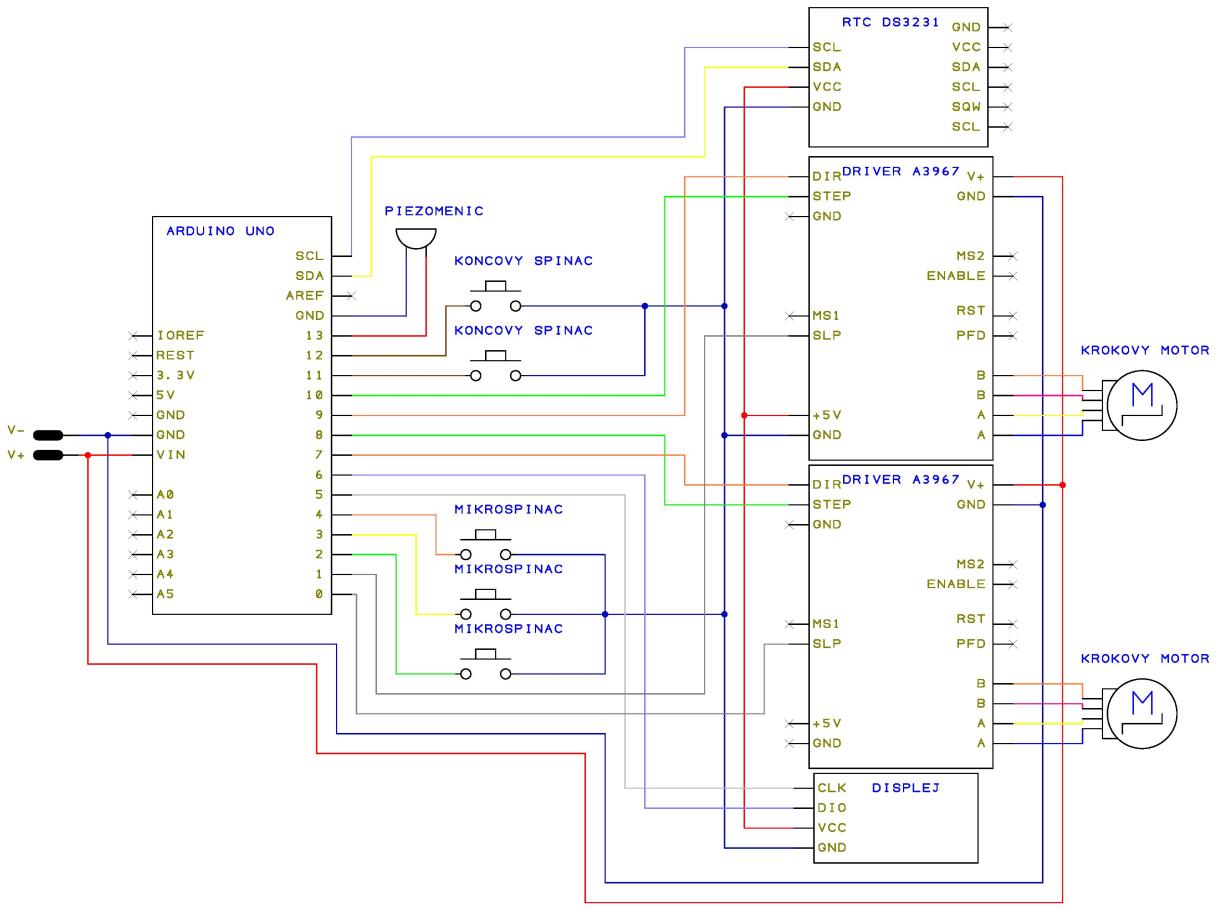
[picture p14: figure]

Obr. 5-1 Schéma zapojení

Pro přehlednost doplňuji tabulku, která shrnuje připojení jednotlivých digitálních a analogových pinů Arduina UNO k modulům a dalším elektrotechnickým součástkám na základě schématu zapojení (viz Obr. 5-1). Taktéž je v tabulce stručně popsána jejich funkce (viz Tab. 5-1).

Označení pinu | Připojená komponenta | Funkce
0, 1 | Driver krokových motorů | Vypnutí driverů krokových motorů
2,3,4 | Mikrospínače | Tlačítka pro ovládání hodin
5,6 | Display | Zobrazení hodnot na displeji
7,9 | Driver krokových motorů | Řízení smyslu otáčení krokových motorů
8,10 | Driver krokových motorů | Řízení natočení krokových motorů
11,12 | Koncové spínače | Polohování hodin
13 | Piezoměnič | Zvuková signalizace alarmu
SDA/A4, SCL/A5 | RTC modul | Měření času
Tab. 5-1 Propojení analogových a digitálních pinů

## 5.2 Konstrukční rozvržení

Prostorové rozmístění jednotlivých elektrotechnických součástek v modelu bylo navrženo především s ohledem na celkové rozměry zařízení a snadnou montáž a demontáž zařízení. Na základě tohoto rozvržení poté budou vymodelované kryty, ve kterých se komponenty připevní pomocí samořezných šroubů.

Zvolil jsem variantu, v níž jsem rozdělil elektrotechnické součástky do dvou řad nad sebou, z důvodu snížení rozměrů. Jednu polovinu potom osadí pouze deska Arduino a ostatní součásti budou připojeny do poloviny druhé. Samotné rozložení druhé poloviny lze lépe vidět na přiloženém schématu (viz Obr. 5-1).

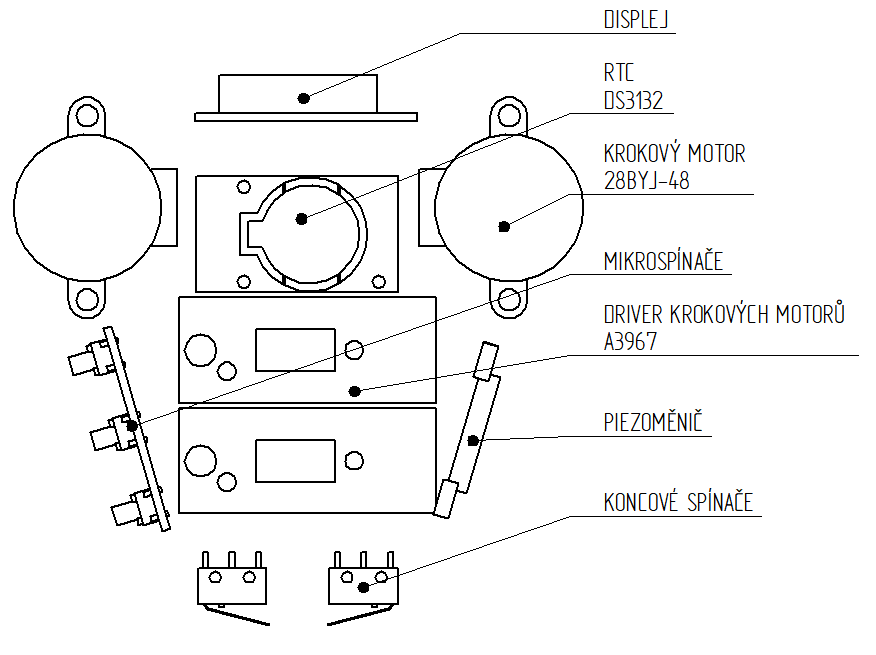
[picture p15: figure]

Obr. 5-2 Konstrukční rozložení elektronických součástí

## 5.3 Návrh krytů

Na základě zamýšleného rozložení elektrotechnických součástí byl vytvořen kryt pro jejich uchycení. Samotný kryt bude dělitelný na dvojici dílů, který se následně spojí samořezným šroubem. U samotného návrhu byl brán zřetel především na nízkou hmotnost a snadnou výrobu. Jelikož zamýšlený způsob výroby finálního prototypu je pomocí 3D tisku je vhodné designovat součást s ohledem na tento způsob výroby, především minimalizovat množství převisů na modelu pro minimalizaci podpůrného materiálu. Většina doporučených rozměrů byla převzata pro plastové součásti vyráběné vstřikováním plastů. [19]

### Upevnění modulů

Všechny moduly, které jsou použity mají předvrtané montážní otvory pro šrouby. Velikosti montážních otvorů uvádím v následující tabulce (viz Tab. 5-2).

Komponenta | Počet otvorů | Průměr montážního otvoru [mm] | Použitý samořezný šroub DIN 7981C
Arduino UNO | 4 | 3,175 | 2,9 x 6,5
RTC modul | 3 | 2,4 | 2,2 x 6,5
Driver krokových motorů | 2 | 3,5 | 2,9 x 6,5
Krokové motory | 2 | 4,2 | 2,9 x 12
Displej | 4 | 2,2 | 2,2 x 6,5
Piezoměnič | 2 | 2,5 | 2,2 x 6,5
Mikrospínače | 2 | 2,5 | 2,2 x 6,5
Koncový spínač | 2 | 2,2 | 2,2 x 8
Souosý konektor | 2 | 2,5 | 2,2 x 6,5
Tab. 5-2 Montáž elektrotechnických součástek

Pro upevnění modulů a dalších elektrotechnických součástek byly využity příslušné samořezné šrouby, které se zašroubovaly do vytvořených montážních nálitků v krytech. Rozměry montážních nálitků byly navrženy podle doporučených hodnot pro plastové součásti. [19] Průměr vnitřní díry (viz Obr. 5-3) u montážního nálitku byl pak určen na základě materiálu a použitého šroubu. [20]

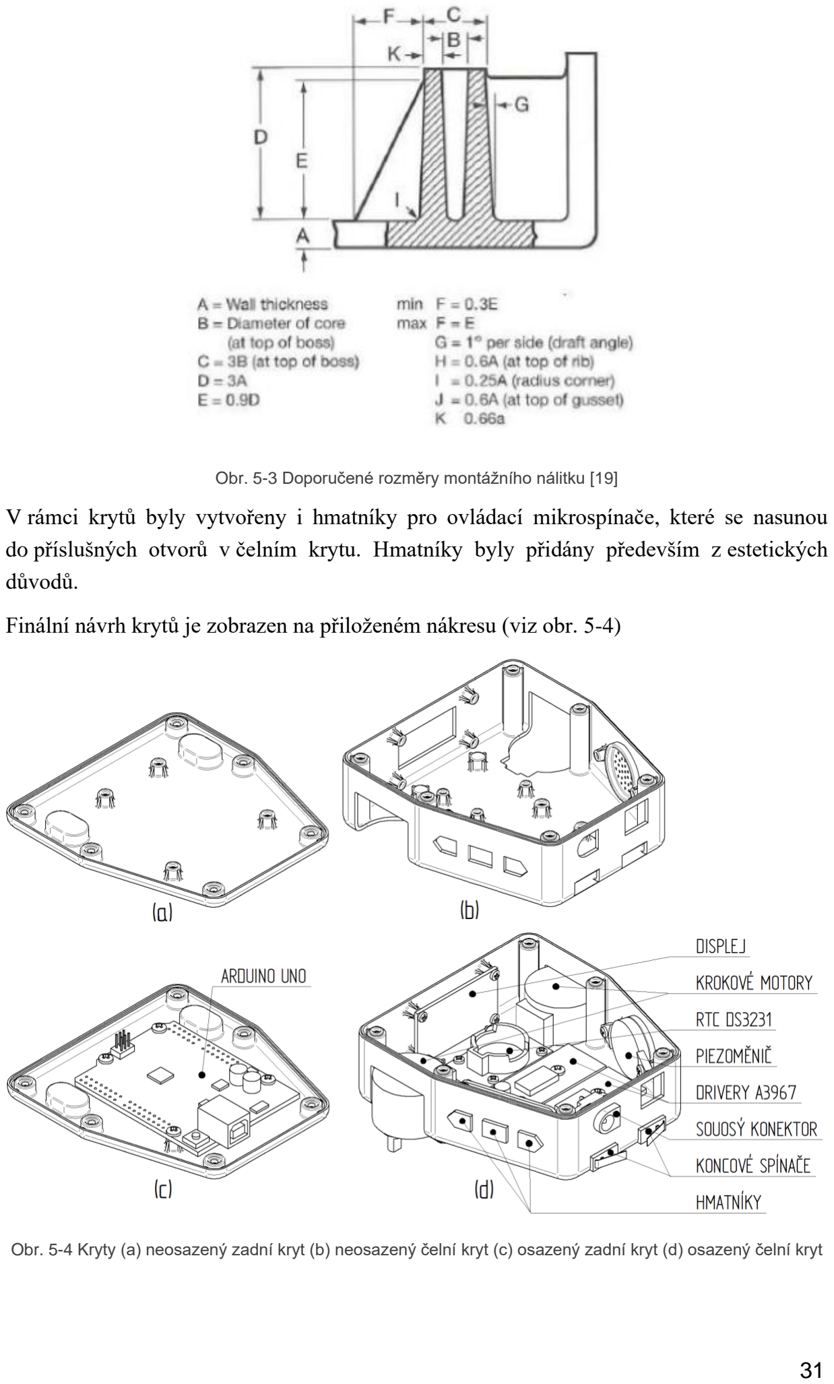
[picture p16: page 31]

Obr. 5-3 Doporučené rozměry montážního nálitku [19]

V rámci krytů byly vytvořeny i hmatníky pro ovládací mikrospínače, které se nasunou do příslušných otvorů v čelním krytu. Hmatníky byly přidány především z estetických důvodů.

Finální návrh krytů je zobrazen na přiloženém nákresu (viz obr. 5-4)

Obr. 5-4 Kryty (a) neosazený zadní kryt (b) neosazený čelní kryt (c) osazený zadní kryt (d) osazený čelní kryt

## 5.4 Převodový mechanismus

Převod ozubeným hřebenem je mechanismus sloužící k transformaci pohybu z rotačního na lineární pohyb. V mém případě jde o transformaci otáčivého pohybu krokových motorů, na jejíchž výstupních hřídelích budou umístěny pastorky, na lineární pohyb ozubených hřebenů uložených v lineárním kluzném vedení (viz Obr. 5-5).

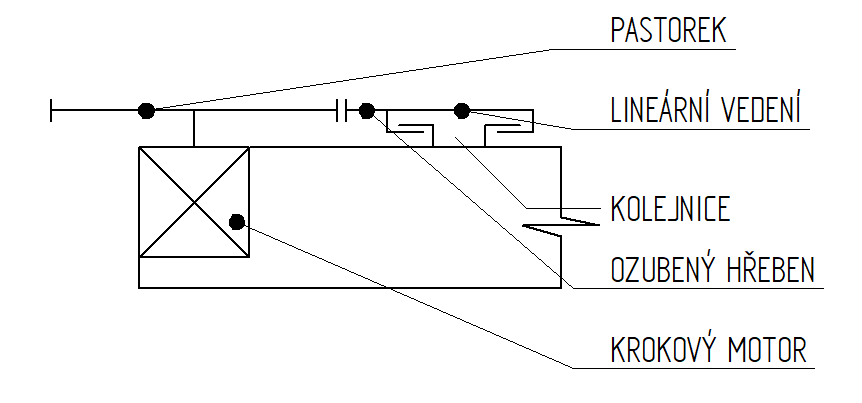
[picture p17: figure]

Obr. 5-5 Schéma převodového mechanismu

### Převod ozubeným hřebenem

Pro návrh čelních ozubených soukolí z oceli existuje řada norem a postupů například norma ČSN ISO 6336 nebo ČSN 01 4686. Výpočty, které se v normách uvádí, jsou detailní

a zohledňují celou řadu vlivů, avšak příliš nekorespondují se skutečností v případě, kdy ocel nahradíme plastem. [21]

Důvodu proč tyto výpočty se odchylují od skutečnosti je hned několik. Při kontrole na ohyb považujeme zub za vetknutý nosník namáhaný prostým ohybem. Předpokladem výpočtu je, že zuby jsou ideálně tuhé a nedeformují se což pro ozubení z plastu neplatí. [21] Kontaktní namáhání je často určováno pomocí Hertzova tlaku. Pro výpočet je nutné znát materiálové charakteristiky jako modul pružnosti a Poissonovo číslo, které se u plastů výrazně liší při změně provozních podmínek jako je teplota, frekvence zatěžování nebo napětí. [21] Pro výpočet se však v zjednodušené formě i nadále používají a slouží pouze jako orientační výpočet.

Jelikož neexistují žádné normy pro pevnostní výpočet pastorku v záběru s ozubeným hřebenem tak je hřeben nahrazen ozubeným kolem s vysokým počtem zubů (1000 zubů). [22]

U pevnostního výpočtu ozubeného hřebenu proběhla pouze zjednodušená kontrola na ohyb v důsledku nedostatečných informací o mechanických vlastnostech vytisknutého materiálu.

Základní vstupní parametry hřebenového převodu nutné pro návrhový výpočet jsou modul mn = 1,5 a počet zubů pastorku, z1 = 20. Výpočtem rozměrových hodnotami ozubeného kola a hřebenu je součástí příloh (viz příloha výpočet převodu).

Pro výpočet obvodové síly se použije následující vztah (5.1):

FT =

2∙M
mn∙z1

=

2∙34,3
1,5∙20
= 2,287 N | (5.1)

Kde FT je obvodová síla udávaná v N, M je jmenovitý kroutící moment krokového motoru v Nmm, mn je modul ozubení, z je počet zubů pastorku.

Výpočet ohybového napětí v patě zubu bude vypočten dle ČSN 01 4686. [23] Výpočet je

zjednodušený a platí pro čelní ozubená kola s přímým a šikmým ozubením. Výpočet se omezuje na ohybového namáhání v patě zubu. [24] Ohybové napětí se vypočte dle vztahu (5.2):

σF =

Ft
mn∙bw
- YF ∙ Yε
- Yβ ≤ σFP | (5.2)

σF =

2,287
1,5∗2
- 2,8 ∙ 0,568 ∙ 1 = 1,212 MPa ≤ 4,9 MPa
kde σF je srovnávací ohybové napětí v patě zubu udávané v MPa, Ft | je obvodová síla
působící na roztečné kružnici v N, mn je normálný modul v mm, bw je účinná šířka zubu v mm, YF je součinitel tvaru zubu, Yε je součinitel vlivu trvání záběru evolventy, Yβ je součinitel sklonu zubu, σFP je přípustné ohybové napětí v patě zubu v MPa.

Součinitel tvaru zubu YF = 2,6 se určí z diagramu (viz příloha výpočet převodu). Součinitel sklonu zubu Yβ = 1 pro přímé ozubení. Součinitel tvaru zubu se spočítá podle vzorce (5.3):

Yε =

1
εα

=

1
1,761
= 0,558 | (5.3)

kde εα je součinitel záběru profilu v čelní rovině pro vnější ozubení (viz příloha výpočet převodu)

Přípustné ohybové napětí σFP = 4,9 MPa. [25]

Pro výpočet bezpečnosti v ohybu SF (5.4) se použijí následující rovnice:

SF =

σFP
σF

=

1,133
4,9
= 4,324 | (5.4)

Ozubené kolo bylo poté i odlehčeno přidáním otvorů. Minimální tloušťka věnce pastorku je navržena podle doporučených hodnot [26] (viz Obr. 5-6) jako dvojnásobek tloušťky zubu na roztečné kružnici.

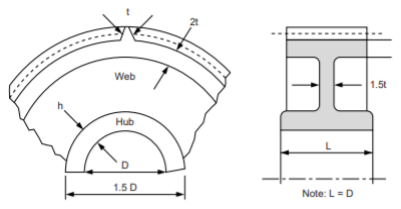
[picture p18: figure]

Obr. 5-6 Doporučené rozměry plastového ozubeného kola [26]

### Vedení

Ozubený hřeben se pohybuje v kluzném lineárním vedení. Navržené vedení je rybinové a je vyrobeno jako jeden díl společně s ozubeným hřebenem. (viz Obr. 5-7).

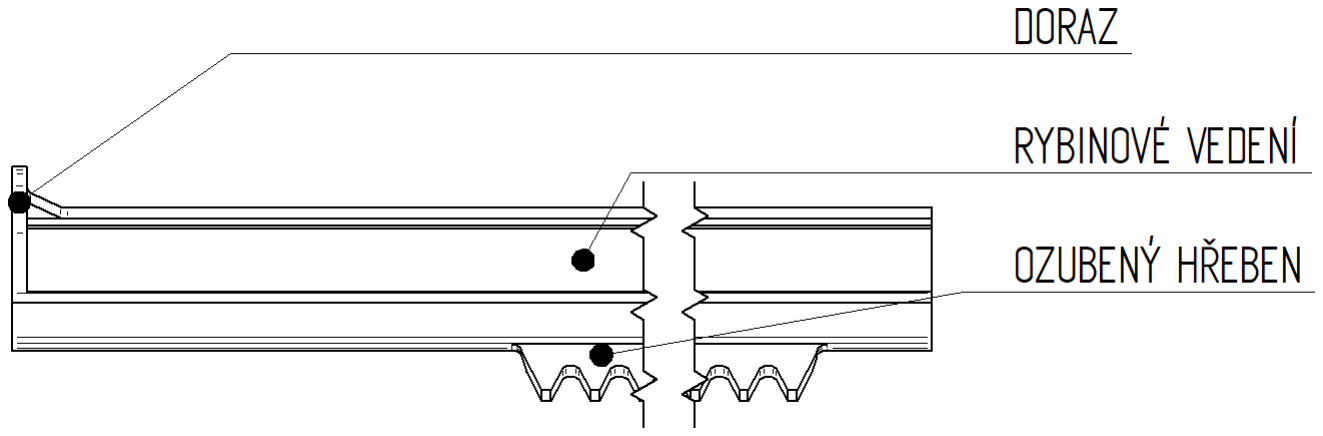
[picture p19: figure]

Obr. 5-7 Návrh ozubeného hřebenu s vedením

Tento díl se pohybuje v kolejnicích, které jsou pevně spojeny s čelním krytem lineárních hodin pomocí samořezných šroubů. Obě kolejnice jsou vyrobeny jako jeden díl a je na něm vytvořen prvek pro uchycení indikátoru (ručičky) (viz Obr. 5-8)

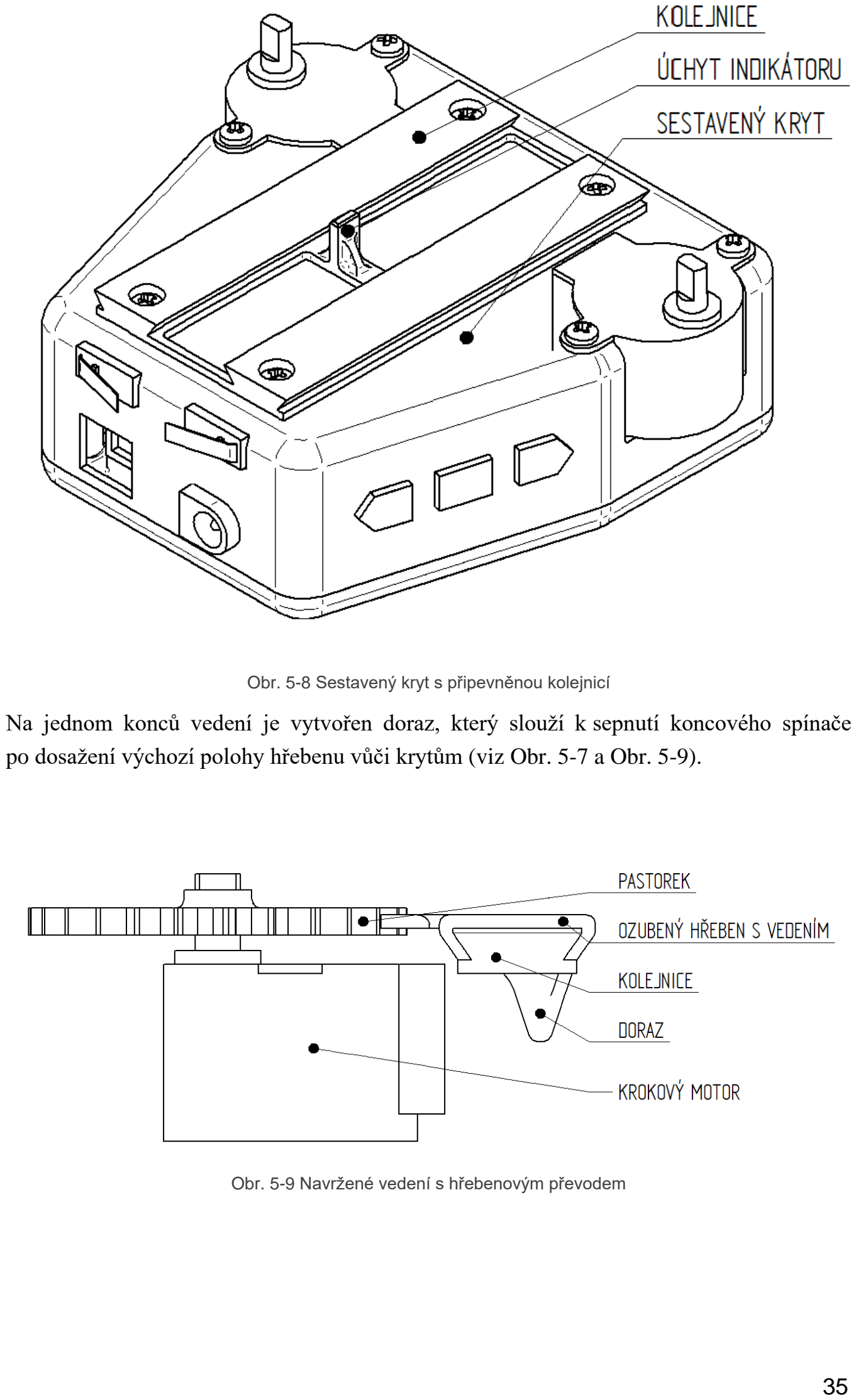
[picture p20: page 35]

Obr. 5-8 Sestavený kryt s připevněnou kolejnicí

Na jednom konců vedení je vytvořen doraz, který slouží k sepnutí koncového spínače po dosažení výchozí polohy hřebenu vůči krytům (viz Obr. 5-7 a Obr. 5-9).

Obr. 5-9 Navržené vedení s hřebenovým převodem

## 5.5 Návrh ciferníků a indikátoru

Ciferníky slouží k zobrazování aktuálního času. Jedná se o dvojici tvarovaných lišt s čísly (viz Obr. 5-10). U hodinového ciferníku jsou to čísla od 0 do 12 a u minutového ciferníku od 0 do 60. Navíc u minutového ciferníku je přidána stupnice ze 60 dílky pro lepší rozlišitelnost lineárních hodin. Vzdálenosti mezi jednotlivými čísly hodin na hodinovém ciferníku jsou poté lhod = 12,5 mm a vzdálenosti mezi jednotlivými dílky minut jsou lmin = 2,5 mm.

Samotně ciferníky jsou pak pevně spojeny k ozubeným hřebenům lepením. Celkové umístění ciferníků vůči ozubeným hřebenům je lépe vidět na přiloženém obrázku (viz Obr. 5-10).

Indikátor je pevně ukotven ke kolejnicím a slouží k určování času. Jedná se o spojení jednoduché šipky pro ukazatel minut a smyčky která slouží pro indikaci minut.

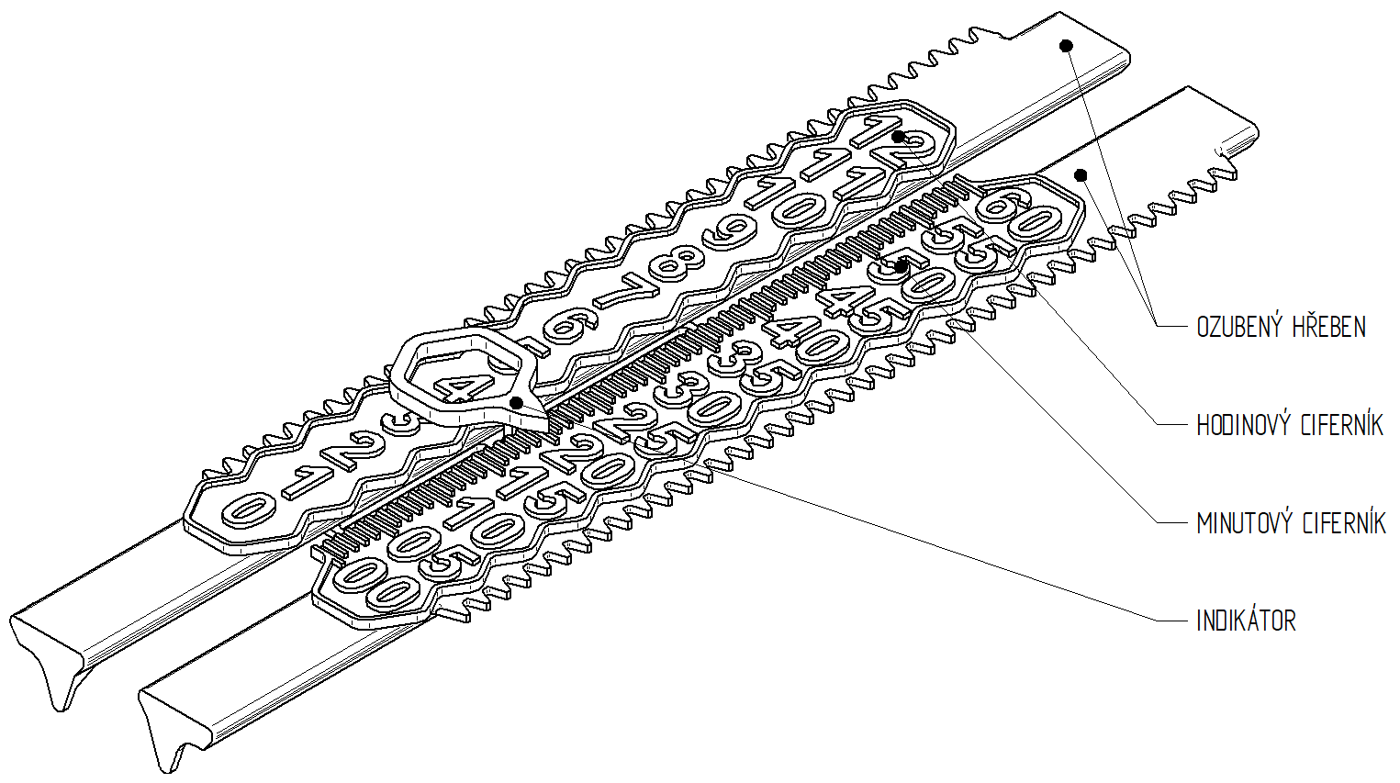
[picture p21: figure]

Obr. 5-10 Ciferníky a indikátor

## 5.6 Výroba

Všechny díly kromě spojujících součástí a řídící elektroniky jsou vyrobeny metodou FDM 3D tisku. Díly byly vyrobeny na 3D tiskárně ENDER 3 V2. Jedná se o levnou, open source 3D tiskárnu od společnosti Creality určenou spíše pro neprůmyslové použití. Maximální rozměry výtisku pak jsou: 220x220x250 mm. Maximální teplota trysky je 260 °C a maximální teplota podložky je 110°C. [27]

### Materiál

Materiál pro kryty elektrotechnických součástí byl zvolen PETG (polyethylene terephthalate glycol) filament od firmy PM Filament. PETG je univerzální pevný a houževnatý materiál, který se vyznačuje dobrou tepelnou stálostí a malým smrštěním při tisku. PETG má výborné mechanické vlastnosti (lepší než ABS) a vyznačuje se snadným tiskem (obdobné jako PLA).
[28] Základní vlastnosti filamentu (tiskové struny) jsou uvedeny v tabulce (viz Tab. 5-3).

Materiál pro hřebenový převod, ciferníky, indikátor a hmatníky bylo zvoleno PLA+ od firmy PM Filament. PLA (polylactic acid) je základní materiál pro tisk, který se vyznačuje především vlastnostmi umožňující snadný a rozměrově přesný tisk. [29] Základní charakteristiky filamentu (tiskové struny) jsou uvedeny v tabulce (viz Tab. 5-3).

Materiál | PETG | PLA+
Průměr filamentu (struny) | 1.75 mm | 1,75 mm
Doporučená teplota trysky | 230–250 °C | 190–210 °C
Doporučená teplota podložky | 60–80 °C | 20–60 °C
Pevnost v ohybu | 1 880 MPa | 3 000 MPa
Hustota | 1,27 g/cm³ | 1,25 g/cm³
Tab. 5-3 Základní vlastnosti použitých plastů [28],[29]

### Nastavení tisku

Samotně zpracování řídícího G-kódu probíhalo v softwaru CURA 4.8.0. Jedná se o bezplatný, open source 3D slicer primárně určený pro 3D tiskárny od firmy Creality. Základní funkcí programu je vygenerování G-kódu na základě vytvořeného 3D modelu. Výrobní časy a množství spotřebovaného materiálu včetně podpor uvádím v tabulce níže (viz Tab. 5-4).

Kompletní G kód všech součásti je pak uveden v přílohách (viz příloha G-kód pro výrobu součástí na 3D tiskárně).

Součást | Spotřebovaný filament [m (g)] | Doba tisku [min]
Kryt – čelní díl | 14,01 (43) | 457
Kryt – zadní díl | 6,24 (19) | 163
Kolejnice | 2,54 (8) | 68
Ozubené hřebeny | 8,28 (25) | 198
Pastorky | 1,53 (5) | 59
Ciferníky, indikátor, hmatníky | 4,65 (14) | 138
Celkem | 37,25 (114) | 1 083
Tab. 5-4 Tisk součástí

## 5.7 Sestavení programu

Program byl vytvořen v programovacím prostředí Arduino IDE ve verzi 1.8.18. Prostředí je primárně určené pro programování platformy Arduino. (viz kapitola 2.3.1)

Základní strukturu programu si můžete pohlédnout na přiloženém vývojovém diagramu (viz Obr. 5-11). Po přivedení napájení se nejdříve provede připojení knihoven, které poskytují dodatečné funkce pro programování jednotlivých modulů jako jsou RTC modul nebo driver krokových motorů. V této části programu se taktéž deklarují proměnné, které budou použity v programu. (viz kapitola 5.7.1) V bloku void setup() se poté provede základní nastavení a uvedení hodin do výchozí polohy. (viz kapitola 5.7.2) V bloku void loop() potom probíhá v nekonečné smyčce hlavní program (viz kapitola 5.7.3). Tento program se skládá ze dvou hlavních větví, a to část programu pro nastavení hodin (viz kapitola 5.7.6) a část pro samotný chod hodin (viz kapitola 5.7.4).

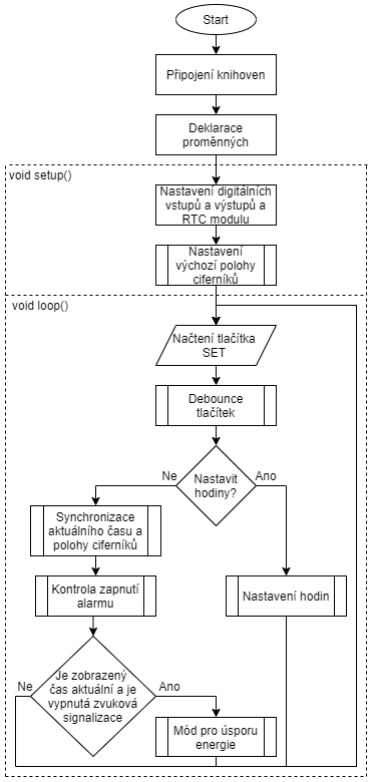
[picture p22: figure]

Obr. 5-11 Vývojový diagram řídícího programu

### Načtení knihoven a deklarace proměnných

První část programu slouží k načtení dodatečných knihoven. Samotné knihovny poskytují dodatečné funkce, které slouží k zjednodušení programování. Knihovna DS3231.h přidává funkce pro práci s RTC modulem především načítání nebo ukládání aktuálního času. Knihovna TM1637Display.h umožňuje snadné a pohodlné formátování displeje. Knihovny avr/sleep.h a avr/wdt.h přidávají funkce pro snížení spotřeby energie.

Nastavení čísel digitálních pinů v programu musí být shodné se schématem zapojení (viz Obr. 5-1), respektive s tabulkou (viz Tab. 5-1).

V této části programu se taktéž deklarují proměnné použitě v celém programu. Úplný

seznam všech deklarovaných proměnných naleznete v přílohách (viz příloha řídící program).

Důležité proměnné jejíchž hodnoty se musí nastavit pro správnou funkci programu, slouží k nastavení rychlosti otáčení krokových motorů a k nastavení počtu kroků, které musí krokový motor vykonat, aby se posunul ciferník vůči indikátoru o vzdálenost jednoho dílku na hodinovém nebo minutovém ciferníku.

Pro zjištění počtu kroků, které jsou nutné, aby motor posunul ciferník, skrze převod ozubeným hřebenem, o danou délku K je u hodinového ciferníku použit odvozený vzorec (5.5):

K =

360°
θm
- i ∙ kř

∙

lℎod
π∗mn∗z

=

360°
11,25°
- 64 ∙ 8 ∙

12,5
π∙1,5∙28
≅ 1 672 | (5.5)

U minutového ciferníku poté vzorec (5.6):

K =

360°
θm
- i ∙ kř

∙

lmin
π∗mn∗z

=

360°
11,25°
- 64 ∙ 8 ∙

2,5
π∙1,5∙28
≅ 334 | (5.6)

kde ϴm je velikost kroku udávána je stupních, i je převodový poměr převodovky motoru, kř koeficient udávající počet mikrokroků na jeden krok, mn je modul ozubení, z je počet zubů pastorku a lhod a lmin je lineární vzdálenost mezi jednotlivými dílky na hodinovém nebo minutovém ciferníku udávané v mm.

Velikost kroku ϴm můžeme nalézt ve specifikacích motoru [15] (viz Tab. 4-2 ).

Některé typy krokových motorů obsahují i převodovku pro zvětšení kroutícího momentu a redukci otáček. Převodovku obsahuje i použitý krokový motor s označením 28BYJ-48. Celkový převodový poměr i = 64 a můžeme jej zjistit ze specifikací motoru [15] (viz Tab. 4-2).

Použitý driver A3967, určen k řízení krokového motoru, je možné nastavit do čtyř typů řízení a to: čtyřtatkní (full-step), osmitaktní (half-step), 1/4 mikrokrokování (1/4-step) a 1/8 mikrokrokování (1/8-step). Přičemž základní nastavení je právě 1/8 mikrokrokování (1/8-step). [16] Při mikrokrokování se právě jednotlivé kroky dělí na další několik mikrokroků v tomto konkrétním případě na 8 menších kroků. Při výpočtu kroků K je nutné zohlednit množství mikrokroků na jeden krok koeficientem kř.

Vzdálenost pohybu ozubeného hřebenu zjistíme z návrhu rozteče jednotlivých hodnot na ciferníku (viz kapitola 5.5). Vzdálenost mezi čísly zobrazující hodiny je zde lhod = 12,5 mm. Vzdálenost mezi čísly zobrazující minuty je zde lmin = 2,5 mm.

Rychlost otáčení krokových motorů se řídí délkou prodlevy mezi jednotlivými impulzy (kroky motoru). Pro přibližné nastavení rychlosti otáčení se použije následující vzorec (5.7): [16]

td =

1
360°
θm

∙i∙kř

∙

n
60∙2

=

1
360°
11,25∙64∙8∙

15
60∙2

≈ 1,22 ∙ 10⁻⁴
s = 122 μs | (5.7)

Kde td čas prodlevy mezi impulzy, ϴm je velikost kroku udávána je stupních, i je převodový poměr převodovky motoru, kř koeficient udávající počet mikrokroků na jeden krok, n je počet otáček v min⁻¹

Počet otáček n je zvolen na 15 ot/min⁻¹

Vzorec udává převrácenou hodnotu počtu kroků, kterou motor vykoná za jednu sekundu při zvolených otáčkách.

### Nastavení zařízení

Po připojení napájení se v bloku void setup() provede základní nastavení programu. V tomto bloku probíhá zejména nastavení vstupů a výstupů pomocí funkce pinMode() [], RTC modulu, aby čas vypisoval ve 24hodinovém formátu, zavolaní dvojice funkcí k posunutí ciferníku do výchozí polohy (viz kapitola 5.7.5) a nastavení hardwarového přerušení (viz Obr. 5-12).

Hardwarové přerušení je způsob, jak obsloužit důležité události. Pokud je nutné na událost okamžitě reagovat, procesor přeruší načítání instrukcí programu a začne načítat program určený pro zpracování přerušení. Jakmile obsluha přerušení skončí, procesor se opět vrátí k původní činnosti. K použití hardwarového přerušení je nutné, aby měl procesor přerušení hardwarově implementované. V případě Arduina UNO jsou to piny 2 a 3. [30]

Obr. 5-12 Nastavení zařízení po zapnutí

### Hlavní struktura programu

Hlavní činnosti nutné pro fungování hodin se nachází v nekonečné smyčce v bloku void loop(). Samotný program se dělí do dvou větví jedna část zajišťuje nastavení hodin a druhá jejich běžný chod. Tato část programu se skládá z podprogramu pro řízený pohyb ciferníků podprogramu pro funkci alarmu a podprogramu pro šetření energií. V hlavním programu se taktéž kontroluje stav prostředního tlačítka, které přepíná mezi jednotlivými nastaveními hodin a vypíná zvukovou signalizaci alarmu.

void setup() {
// nastavení pinů jako výstupních pinMode(DIR_MIN, OUTPUT);
pinMode(STEP_MIN, OUTPUT); pinMode(DIR_HOD, OUTPUT);
pinMode(STEP_HOD, OUTPUT); pinMode(SLP_HOD, OUTPUT);
pinMode(SLP_MIN, OUTPUT);
pinMode(BUZZER, OUTPUT);

// připojení obou řídících pinů na zem digitalWrite(DIR_HOD, LOW); digitalWrite(STEP_HOD, LOW); digitalWrite(DIR_MIN, LOW); digitalWrite(STEP_MIN, LOW);

digitalWrite(SLP_HOD, LOW); digitalWrite(SLP_MIN, LOW);

// nastavení pinů jako vstupních pinMode(SET_TIME, INPUT_PULLUP); pinMode(UP_TIME, INPUT_PULLUP); pinMode(DOWN_TIME, INPUT_PULLUP); pinMode(KON_HOD, INPUT_PULLUP);
pinMode(KON_MIN, INPUT_PULLUP);

RTC.setClockMode(false); //nastavení 24 hodinového formátu času

//funkce pro hardwarové přerušení právě probíhajícího programu //na základě stisknutí tlačítka SET attachInterrupt(digitalPinToInterrupt(SET_TIME), Vzbudit, RISING);

//Nastavení výchozí polohy
HomeHod();
HomeMin();
}

### Synchronizace

Tato část programu slouží pro řízený pohyb ciferníku tak aby aktuální čas byl shodný z časem zobrazeným. Strukturu programu si můžete prohlédnou na přiloženém vývojovém diagramu (viz Obr. 5-13). Program načte aktuální hodnotu minut a hodin z RTC modulu uloží ji do proměnných (Hodiny, Minuty) a převede ji na 12hodinový formát. Následně
se provede | porovnání | aktuálního | (Hodiny, | Minuty) | a | zobrazeného | času
(HodinyPol, MinutyPol). Pokud aktuální hodnota času je větší, než hodnota zobrazená provádí se posun ciferníku tak dlouho dokud se rozdíl nevyrovná. Pokud je situace opačná tak nastane posun zpět do výchozí pozice.

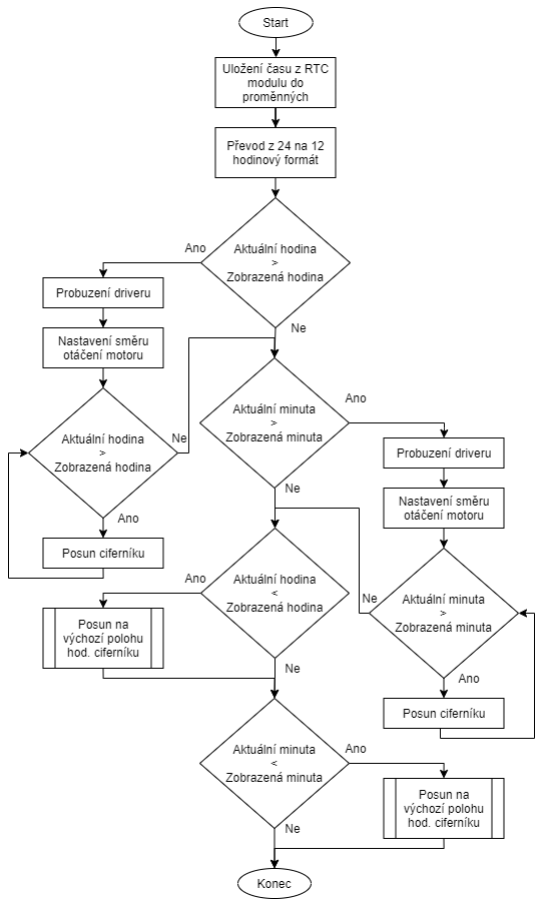
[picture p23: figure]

Obr. 5-13 Program pro synchronizaci změřeného a zobrazovaného času

### Nastavení výchozí polohy

Tento podprogram slouží k nastavení výchozí poloh ciferníků. Strukturu programu je možné vidět na přiloženém schématu (viz Obr. 5-14). Po zavolání podprogramu se spustí motory a posouvání ozubený hřeben směrem ke koncovým spínačům, dokud je nesepnou. Po jejich sepnutí se nastaví výchozí (nulová) hodnota polohy ciferníků a uloží se do proměnných (HodinyPol = 0, MinutyPol = 0).

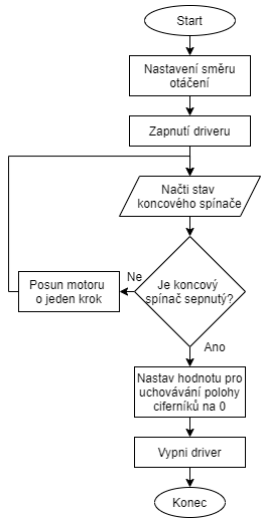
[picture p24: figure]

Obr. 5-14 Nastavení výchozí polohy ciferníků

### Nastavení hodin

Podprogram slouží k přenastavení aktuálního času a nastavení času a zapnutí alarmu. Podprogram načte aktuální čas z RTC modulu a rozsvítí se displej s nápisem „SET“ pro indikaci možnosti nastavení času. Po vteřině se zobrazený nápis změní na čas, který je uložen v RTC modulu. Uživatel zde bude moct přenastavit čas. Samostatné nastavení je rozděleno času je rozděleno do dvou kroků, a to nastavení hodin a nastavení minut. Hodnota času, která se nastavuje pro zvýraznění problikává. Zvyšování nebo snižování hodnoty potom probíhá krajními tlačítky. Přepínání mez dalšími nastaveními probíhá stisknutím prostředního tlačítka. Po dokončení nastavení času se hodnota zapíše do RTC modulu a podprogram pokračuje nastavením alarmu zobrazením nápisu ALR na displeji.

Nastavení času alarmu probíhá obdobným způsobem nastavením hodin a minut a potvrdí se opět prostředním tlačítkem. Po dokončení nastavení času zapnutí alarmu se objeví nastavení, zda alarm má být zapnut. Uživatel tuto hodnotu může nastavit pomocí krajních tlačítek. Na displeji se objeví nápis „OFF“ když je alarm neaktivní nebo nápis „ON“, když se alarm aktivuje. Po stisknutí prostředního tlačítka se nastavení alarmu uloží a displej zhasne.

Pokud při nastavování času dojde k absenci jakéhokoliv vstupního signálu po dobu delší jak jednu minutu, tak se automaticky celé nastavení času ukončí a doposud nastavené hodnoty se uloží. Vývojové schéma je zobrazeno na přiloženém diagramu (viz Obr. 5-15)

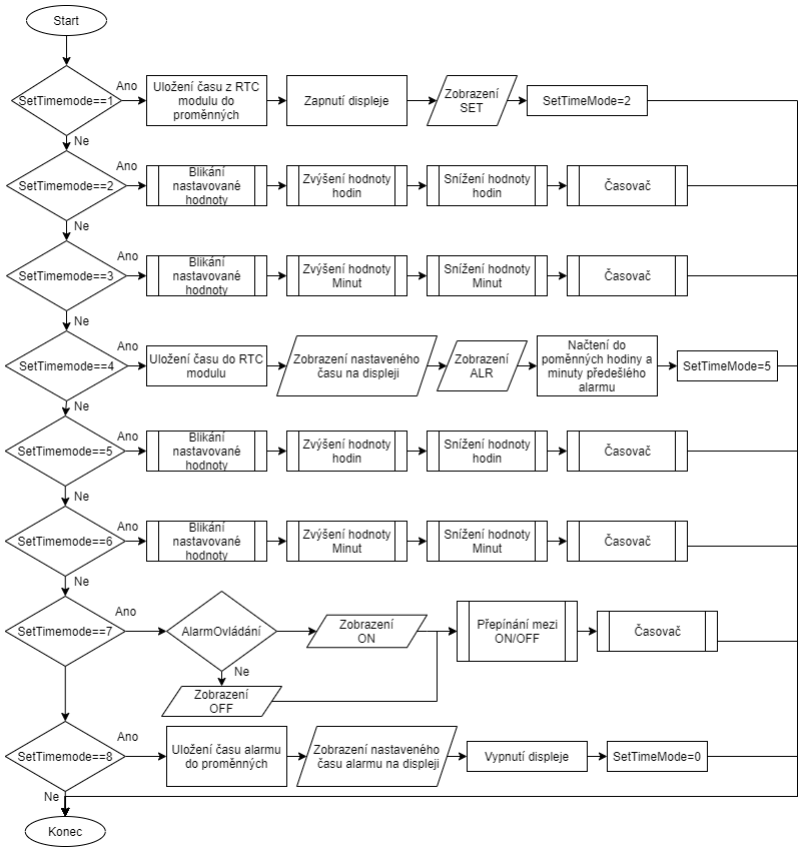
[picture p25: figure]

Obr. 5-15 Nastavení času

### Alarm

Tento program slouží k ověření, zda se má zapnout zvuková signalizace. Schématický můžete jeho funkci vidět na přiloženém vývojovém diagramu. (viz Obr. 5-16). Fungování tohoto podprogramu je velice jednoduché. Provede se kontrola, zda je povolena funkce alarmu a následně se srovná nastavený čas kdy se má alarm spustit s aktuálním časem. Pokud budou podmínky splněny zvuková signalizace se sepne až do doby, dokud se nestiskne tlačítko SET k vypnutí alarmu.


Obr. 5-16 Alarm

### Ošetření zákmitů tlačítek

Pod pojmem ošetření zákmitů tlačítek (tzv. debounce tlačítek) se rozumí ošetřit vstupy proti nechtěným zákmitům při stisku mikrospínače. Jelikož při stisku a rozepnutí mechanického kontaktu membránových tlačítek, mikrospínačů, jazýčkových kontaktů atd., nedojde okamžitě k trvalému sepnutí či rozepnutí kontaktů, ale dochází k zákmitům, po dobu jednotek až desítek milisekund, kdy je obvod kontaktem opakovaně spínán a rozepínán. [31] Tento jev by mohlo vést k napočítání více sepnutí, než bylo tlačítko skutečně stisknuto. Proto je vhodné vstupy ošetři. Ošetření je možno provádět hardwarově například použitím filtračního RC obvodu anebo softwarově. U softwarového ošetření, které je použito v mém případě, se provádí tak, že po zaznamenání prvního stisku tlačítka se zakáže opakované stisknutí po krátkou dobu například 100 ms, což zabrání nechtěným napočítání stisků.

### Spotřeba energie

Tento podprogram má za úkol snížit spotřebu energie na minimum. Jeho úkolem je vypnout všechny nepotřebné prvky Arduina. [32] Vypnutí tohoto módu probíhá současně dvěma způsoby a to každých 8 sekund vnitřním časovačem anebo po stisku prostředního tlačítka díky nastavenému hardwarovému přerušení.

Výsledné snížení energie je patrné v přiložené tabulce (viz Tab. 5-1).

Režim chodu | Spotřeba proudu [mA]
Chod hodin (motory jsou v chodu) | 440
Pohotovostní režim (motory pod napětím) | 400
Drivery vypnuty | 76,5
Mód pro úsporu energie | 37,50
Tab. 5- 5 Změřená spotřeba energie

## 5.8 Sestavení lineárních hodin

Sestavení probíhalo od osazení krytů elektrotechnickými součástmi (viz Obr. 5-4) a spojení jednotlivých součástí pomocí propojovacích vodičů podle schématu zapojení (viz Obr. 5-1). Po propojení elektrotechnických součástí a otestování funkčnosti sestaveného programu se obě poloviny krytů spojily samořeznými šrouby. Ke krytům se upevnily kolejnice pomocí samořezných šroubů (viz Obr. 5-8). Na tyto kolejnice se nasunuly ozubené hřebeny s ciferníky, které jsou na hřebeny připevněny pomocí lepení. (viz Obr. 5-10). Posledním krokem sestavení bylo nasunutí pastorků na výstupní hřídele krokových motorů. Finální konstrukci lineárních hodin poté můžeme vidět na přiloženém obrázku (viz Obr. 5-17).


Obr. 5-17 Sestavené lineární hodiny

## 5.9 Náklady

Všechny elektronické součásti jsou nakoupeny výhradně z české distribuce a jednotlivé ceny modulů a elektrotechnických součástí jsou uvedeny v následující tabulce (viz Tab. 5-6).

Elektrotechnická součástka | Cena za kus [Kč]
Arduino Uno (klon) | 159
2 x Driver krokových motorů | 71
2 x Krokový motor 28byj-48 | 59
RTC modul DS3231 | 65
Displej | 39
2 x koncový spínač | 10
3 x mikrospínač | 2,70
Piezoměnič | 19
Souosý konektor | 7,30
Tab. 5-6 Cena elektrotechnických součástek

Spojující součásti jsou výhradně samořezné šrouby a jejich náklady jsou uvedeny v následující tabulce (viz Tab. 5-7).

Počet kusů | Označení šroubu | Cena za kus [Kč]
13 | 2,2 x 6,5 | 1,10
4 | 2,2 x 8 | 1,20
12 | 2,9 x 6,5 | 1,20
10 | 2,9 x 12 | 0,30
Tab. 5-7 Cena samořezných šroubů

Náklady na všechny vyrobené součásti pomocí 3D tisku jsou uvedeny v následující tabulce (viz Tab. 5-8).

Součást | | Cena Materiálu [Kč]
Kryt – čelní díl | 25,80
Kryt – zadní díl | 11,40
Kolejnice | 7,10
Ozubené hřebeny | 11,40
Pastorky | 2,60
Ciferníky, indikátor, hmatníky | 6,30
Tab. 5-8 Cena materiálu vyrobených dílců

Sečtení všech dílčích nákladů a celkové náklady jsou uvedeny v tabulce níže (viz Tab. 5-9).

Náklady | Cena [Kč]
Náklady za elektronické součásti | 440,40
Náklady za spojovací součásti | 36,50
Náklady za materiál | 64,60
Celkové náklady | 541,50
Tab. 5-9 Celkové náklady

## 6 DISKUZE

Při vytváření finálního řešení lineárních hodin jsem především vycházel ze současných řešení, které jsem modifikoval tak, aby došlo ke snížení rozměrů, hmotnosti a nákladů s přihlédnutím ke způsobu výroby pomocí 3D tisku. Většina navržených řešení vycházela ze společné posloupnosti konstrukčních uzlů: Výběr elektrotechnických součástek, návrh upevnění a zakrytování elektrosoučástek, návrh mechanismu převádějící rotační pohyb na lineární, návrh ciferníku a indikátoru a sestavení řídícího programu.

Vybrané koncepční řešení bylo zvoleno především na základě snadné výroby všech součástí mechanismu pomocí 3D tisku.

Pro následný konstrukční návrh bylo nutné zvolit potřebné funkce lineárních hodin a podle nich zvolit příslušnou řídící elektroniku. Pro elektroniku bylo nutné navrhnout kryty, které jej budou chránit před okolními vlivy a upevní je ke konstrukci. U návrhu krytů nejdříve proběhla rozvaha o vhodném umístění jednotlivých komponent v prostoru, aby celkové rozměry krytů byly co nejmenší. Podle tohoto rozložení pak vznikly finální rozměry krytů. Převodový mechanismus byl navržen na základě značně zjednodušeného pevnostního výpočtu ozubeného kola a hřebenu. K tomuto mechanismu bylo pak vytvořeno uložení v lineárním kluzném vedení. Následné navržení ciferníků a indikátoru (ručičky) byla již ryze designérská práce limitovaná pouze délkou ozubeného hřebenu.

Výroba jednotlivých navržených součástí probíhala na 3D tiskárně. Celková doba tisku všech součástí byly 18,05 hodiny a spotřebovalo se 37,25 metrů filamentu.

Vytvoření řídícího programu probíhalo v Arduino IDE. Program musel zajišťovat všechny potřebné funkce hodin od měření a zobrazování času přes funkci alarmu až po nastavení hodin.

Hodiny je nutné napájet zdrojem o napětí v rozmezí 6,5-20 V.

Výkresová dokumentace vyrobených součástí, G-kódy pro výrobu navržených dílů pomocí 3D tisku a řídící program je součástí příloh této práce.

## 7 ZÁVĚR

Hlavní cíl práce byl navrhnout a vyrobit za pomocí 3D tisku model lineárních hodin řízené mikrokontrolerem Arduino UNO.

Dílčími cíli bylo analyzovat problém a provést rešerši současných konstrukčních řešení lineárních hodin, vypracovat možné koncepční návrhy a jeden z nich vybrat a dále návrh rozpracovat do podoby kompletního funkčního modelu.

V teoretické částí práce jsou nastíněny některá současná konstrukční řešení, z těchto designů je poté v praktické části čerpáno, především v oblasti výběru elektrotechnických součástí. Obsahem rešerše je navíc i analýza platformy Arduino s popisem jeho vývojového prostředí a vývojové desky použité ve finálním modelu lineárních hodin.

Finální model hodin obsahuje dvojici ciferníků pro zobrazování hodin a minut odděleně. Rozlišitelnost hodin je 1 minuta. Model lineárních hodin plní základní funkce jako je měření a zobrazování času, funkce přenastavení času a funkce alarmu Celkové rozměry hodin jsou 240 mm x 140 mm x 140 mm s hmotností přibližně 250 g. Hodiny jsou napájeny skrze souosý konektor a jejich spotřeba je 34 mA při vypnutých motorech.

Dalším možným vylepšením hodin by bylo přidání baterií, ale současná spotřeba u tohoto modelu je příliš velká na udržení hodin v chodu přijatelnou dobu skrze baterie. Řešením

by bylo zaměnit Arduino UNO a ostatní moduly za jiný obvod, který by byl navrhnut s ohledem na co nemenší spotřebu energie a snížení nákladů. Popřípadě zaměnit krokové motory za učenější a levnější systém pohonu.

## 8 SEZNAM POUŽITÝCH ZDROJŮ

[1] Time. The free dictionary [online]. Feasterville: Farlex, © 2021 [cit. 2021-5-5]. Dostupné z: www.thefreedictionary.com/time
[2] SI base unit: second (s). BIPM [online]. Paris: BIPM, 2019 [cit. 2021-5-5]. Dostupné z: https://www.bipm.org/en/si-base-units/second
[3] Hodiny. Wikipedia: the free encyclopedia [online]. San Francisco (CA): Wikimedia Foundation, 2021 [cit. 2021-1-5]. Dostupné z: https://cs.wikipedia.org/wiki/Hodiny
[4] TORROJA, Juan. Mechanism of linear clocks. Spojené státy americké. US2333832A.
Přihlášeno | 28.11.1941. | Uděleno | 9.11.1943. | Dostupné | také | z:
https://patents.google.com/patent/US2333832
[5] CLOQ: The linear clock [online]. United Kingdom: Rob Lafratta, © 2021 [cit. 2021-2-30]. Dostupné z: http://thelinearclock.co.uk/
[6] Linear clockworks [online]. Asheville, NC: Lindsay Morris, © 2021 [cit. 2021-2-31]. Dostupné z: http://linearclockworks.com/
[7] Linear clock. [online]. Nizozemsko: Jan Derogee, [2018] [cit. 2021-1-7]. Dostupné z: http://home.kpn.nl/bderogee1980/projects/linear_clock/linear_clock.html
[8] Linear Clock. Instructables [online]. San Francisco: Euphy, 2011 [cit. 2021-2-5]. Dostupné z: https://www.instructables.com/Linear-Clock/
[9] The linear clock. Gessato [online]. New York: Audun Ask Blaker, © 2021 [cit. 2021-2-6]. Dostupné z: https://www.gessato.com/the-linear-clock-by-audun-ask-blaker/
[10] VODA, Zbyšek. Průvodce světem Arduina. Vydání druhé. Bučovice: Martin Stříž, 2017. ISBN 978-80-87106-93-8.
[11] ARDUINO UNO REV3. Arduino store [online]. Chiasso: Arduino, © 2021 [cit. 2021-2-5]. Dostupné z: https://store.arduino.cc/arduino-uno-rev3
[12] ESES. [online katalogový list]. eses klon Arduino UNO R3 CH340. ©2021 [cit. 2021-2-5]. Dostupné z: https://dratek.cz/docs/produkty/0/761/eses1459967190.pdf
[13] SKALICKÝ, Jiří. Elektrické servopohony. Vyd. 2. Brno: Vysoké učení technické,

2001. ISBN 80-214-1978-4.

[14] SEMRÁD, M. Řízení krokových motorků. Brno: Vysoké učení technické v Brně,

Fakulta elektrotechniky a komunikačních technologií, 2012. 47s. Vedoucí bakalářské práce byl Ing. Lukáš Kopečný, Ph.D.

[15] Kiatronics. [online katalogový list]. 28BYJ-48. ©2021 [cit. 17.2.2021]. Dostupné z: https://datasheetspdf.com/pdf/1006817/Kiatronics/28BYJ-48/1
[16] Easy Driver Stepper Motor Driver. Schmalz Haus LLC [online]. Schmalz Haus, © 2021 [cit. 2021-2-20]. Dostupné z: https://bit.ly/3h67uR6
[17] ECLIPSERA MODULELS. [online katalogový list]. RTC Hodiny reálného času DS3231. ©2021 [cit. 17.2.2021]. Dostupné z: https://bit.ly/3b65Uea
[18] EEPROM. Wikipedia: the free encyclopedia [online]. San Francisco (CA): Wikimedia Foundation, 2021 [cit. 2021-5-5]. Dostupné z: https://en.wikipedia.org/wiki/EEPROM
[19] Romeo RIM [online]. Reaction Injection Molding Design Guide, © 2021 [cit. 2021-2-8]. Dostupné z: https://bit.ly/3vGS36b
[20] Boss design. Secam-fixing [online]. MARNAZ: SECAM, © 2021 [cit. 2021-2-15]. Dostupné z: http://secam-fixing.com/screws/boss-design/
[21] DYMÁČEK, M. Plastová ozubená kola a jejich analýza pomocí MKP. Brno: Vysoké

učení technické v Brně, Fakulta strojního inženýrství, 2006. 37 s. Vedoucí bakalářské práce Ing. Martin Vrbka, Ph.D.

[22] Evolventní ozubení. MITCalc [online]. Děčín: Miroslav Petele, Ing., © 2003 - 2021 [cit. 2021-5-5]. Dostupné z: https://mitcalc.com/doc//gear1/help/cz/gear_theory.htm (https://mitcalc.com/doc/gear1/help/cz/gear_theory.htm)
[23] ČSN 01 4686. Pevnostní výpočet čelních a kuželových ozubených kol. Praha: Úřad pro

normalizaci a měření, 1988.

[24] KVĚTOUN, Jan. Porovnání možností výroby ozubených kol kovových a plastových.

Brno, 2017. 40s, 6 příloh, CD. Bakalářská práce. Vysoké učení technické v Brně, Fakulta strojního inženýrství. Ústav strojírenské technologie, Odbor technologie

tváření kovů a plastů. Vedoucí práce Ing. Bohumil Kandus

[25] EZEH, O.H. a L. SUSMEL. On the fatigue strength of 3D-printed polylactide (PLA). Procedia Structural Integrity [online]. 2018, 9, 29-36 [cit. 2021-5-5]. ISSN 24523216. Dostupné z: https://www.sciencedirect.com/science/article/pii/S2452321618300076
[26] DuPont [online]. General Design Principles for DuPont Engineering Polymers, © 2021 [cit. 2021-3-5]. Dostupné z: https://bit.ly/3tomZqi

[27] Creality ENDER 3. CREALITY [online]. Blansko: CREALITY STORE, © 2021 [cit. 2021-5-5]. Dostupné z: https://www.crealitystore.cz/p/ender3/
[28] PETG. Filament PM [online]. Haňovice: Filament PM, © 2021 [cit. 2021-5-5]. Dostupné z: https://www.filament-pm.cz/petg
[29] PLA+. Filament PM [online]. Haňovice: Filament PM, © 2021 [cit. 2021-5-5]. Dostupné z: https://www.filament-pm.cz/PLA%2B
[30] AttachInterrupt(). Arduino [online]. © 2021 [cit. 2021-5-5]. Dostupné z: https://bit.ly/3uqeHQ3
[31] Debounce. | Arduino | [online]. | © | 2021 | [cit. | 2021-5-5]. | Dostupné | z:
https://www.arduino.cc/en/Tutorial/BuiltInExamples/Debounce
[32] Power saving techniques for microprocessors. Gammon Software Solutions [online]. Nick Gammon, 2012 [cit. 2021-3-5]. Dostupné z: http://www.gammon.com.au/power
[33] SHIGLEY, Joseph Edward, Charles R. MISCHKE a Richard G. BUDYNAS, VLK, Miloš, ed. Konstruování strojních součástí. Přeložil Martin HARTL. V Brně: VUTIUM, 2010. Překlady vysokoškolských učebnic. ISBN 978-80-214-2629-0.

## 9 SEZNAM POUŽITÝCH ZKRATEK, SYMBOLŮ A VELIČIN

## 9.1 Použité symboly

aw | osová vzdálenost
bw | účinná šířka ozubení
cn | hlavová vůle
d1, d2 | průměr roztečná kružnice pastorku a kola
da1, da2 | průměr hlavová kružnice pastorku a kola
db1, db2 | průměr základní kružnice pastorku a kola
df1, df2 | průměr patní kružnice pastorku a kola
dw1, dw1 | průměr valivé kružnice pastorku a kola
E | Modul pružnosti v tahu
en | šířka zubové mezery
Fn | normálná síla
Fr | radiální síla
FT | tečná síla
ℎ | výška zubu
ℎa | výška hlavy zubu
ℎf | výška paty zubu
i | převodový poměr vestavěné převodovky v motoru
K | počet kroků motoru
kř | počet mikrokroků na krok
lℎod | rozteč mezi dílky na hodinovém ciferníku
lmin | rozteč mezi dílky na minutovém ciferníku
M | Kroutící moment krokového motoru
mn | modul
mt | tečný modul
n | počet otáček korkového motoru
pb | základní rozteč
pf | poloměr zaoblení přechodové křivky
pn | rozteč
SF | faktor bezpečnosti pro pevnost v ohybu
sn | tloušťka zubu na roztečné kružnici
td | délka prodlevy
u | převodový poměr

v1 | rychlost otáčení pastorku
x1, x2 | jednotkové posunutí
YF | součinitel tvaru zubu
Yβ | součinitel sklonu zubu
Yε | součinitel vlivu trvání záběru evolventy
z1, z2 | počet zubů pastorku a kola
α | úhel záběru
αt | úhel záběru čelní
αtw | valivý úhel záběru čelní
β | úhel sklonu zubů
εα | součinitel záběru v čelní rovině
εβ | součinitel záběru v osové rovině
εγ | součinitel celkového záběru
θm | velikost kroku
μ | Poissonovo číslo
σF | napětí v patě zubu
σFP | dovolené napětí v patě zubu

## 9.2 Použitě zkratky

RTC | modul reálného času

## 10 SEZNAM TABULEK

## 11 SEZNAM OBRÁZKŮ A GRAFŮ

Obr. 2-5 Design lineárních hodin by Audun Ask Blaker (a) design hodin (b) vnitřní

Obr. 5-4 Kryty (a) neosazený zadní kryt (b) neosazený čelní kryt (c) osazený zadní kryt (d)

## 12 SEZNAM PŘÍLOH

Výkresová dokumentace

Řídící program

G-kód pro výrobu součástí na 3D tiskárně

Výpočet převodu

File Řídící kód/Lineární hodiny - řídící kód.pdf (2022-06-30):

1 | //Lineární hodiny
2 | //Marek Firla
3
4 | // připojení potřebných knihoven
5 | //#include <Arduino.h> //knihovny použité při ladění programu
6 | //#include <Wire.h>
7 | #include <DS3231.h> //knihovna zajišťující funkci modulu reálného času
8 | #include <TM1637Display.h> //knihovna pro ovládání displeje
9 | #include <avr/sleep.h> //knihovny pro uspání Arduina
10 | #include <avr/wdt.h>
11
12 | // nastavení čísel propojovacích pinů
13 | #define SLP_HOD 0
14 | #define SLP_MIN 1
15 | #define DOWN_TIME 2
16 | #define SET_TIME 3
17 | #define UP_TIME 4
18 | #define CLK 5
19 | #define DIO 6
20 | #define DIR_HOD 7
21 | #define STEP_HOD 8
22 | #define DIR_MIN 9
23 | #define STEP_MIN 10
24 | #define KON_HOD 11
25 | #define KON_MIN 12
26 | #define BUZZER 13
27
28 | TM1637Display display(CLK, DIO); // vytvoření instance displej z knihovny
29 | TM1637
30 | DS3231 RTC; // inicializace RTC z knihovny
31
32 | //deklarace proměnných
33 | int Hodiny; // proměnná uchovávající aktuální Hodinu
34 | int Minuty; // proměnná uchovávající aktuální minutu
35 | bool h12; // logická proměnná pro nastavení 24 nebo 12 hodinového formátu
36 | bool PM; | // logické proměnná pro rozlišení dopolední a odpoledního času
37 | int HodinyPol; // proměnná uchovávající aktuální polohu hodinového
38 | ciferníku vůči indikátoru
39 | int MinutyPol; // proměnná uchovávající aktuální polohu hodinového
40 | ciferníku vůči indikátoru
41 | int HodinyAlarm; // proměnná uchovávající čas alarmu
42 | int MinutyAlarm;
43 | bool AlarmOvladani = false; //logická proměnná pro zapnutí nebo vypnutí
44 | alarmu
45 | bool AlarmStav = false; //logická proměnná indikující stav zvukové
46 | signalizace
47
48 | // proměnné sloužící pro ošetření zákmitů tlačítek
49 | int enStiskSetTime = 1; | // proměnná povolení stisku
50 | long stiskMilSetTime = 0; | // proměnná pro čas stisku
51 | int stiskSetTime = LOW; | // proměnná pro kontrolu stisku
52 | int stavTlacSetTime = 0; | // proměnná stavu tlačítka
53
54 | int enStiskUpTime = 1; | // proměnná povolení stisku
55 | long stiskMilUpTime = 0; | // proměnná pro čas stisku
56 | int stiskUpTime = LOW; | // proměnná pro kontrolu stisku
57 | int stavTlacUpTime = 0; | // proměnná stavu tlačítka
58
59 | int enStiskDownTime = 1; | // proměnná povolení stisku
60 | long stiskMilDownTime = 0; | // proměnná pro čas stisku
61 | int stiskDownTime = LOW; | // proměnná pro kontrolu stisku

62 | int stavTlacDownTime = 0; | // proměnná stavu tlačítka
63
64 | int stavTlacKonHod = 0; | // proměnná stavu tlačítka
65 | int stavTlacKonMin = 0; | // proměnná stavu tlačítka
66
67 | int KrokyMin = 334; | //proměnná pro počet kroků motoru pro lineární posun o
68 | rozestup jednotlivých označení minut na ciferníku
69 | int KrokyHod = 1672; //proměnná pro počet kroků motoru pro lineární posun o
70 | rozestup jednotlivých označení hodin na ciferníku
71
72 int Rychlost = 122; //přepočet na délku mezery mezi impulzy
73
74 int SetTimeMode = 0; //proměnná pro přepínání módů nastavení hodin
75
76 | //hodnoty pro informativní nápisy na displeji
77 | const uint8_t SEG_SET[] = {
78 | SEG_A | SEG_F | SEG_G | SEG_C | SEG_D , | // S
79 | SEG_A | SEG_F | SEG_G | SEG_E | SEG_D , | // E
80 | SEG_F | SEG_G | SEG_E | SEG_D , | // T
81 | 0x00 ,
82 | };
83
84 | const uint8_t SEG_ON[] = {
85 | SEG_A | SEG_F | SEG_E | SEG_D | SEG_C | SEG_B , | // O
86 | SEG_E | SEG_G | SEG_C | SEG_E , | // N
87 | 0x00 ,
88 | 0x00 ,
89 | };
90
91 | const uint8_t SEG_OFF[] = {
92 | SEG_A | SEG_F | SEG_E | SEG_D | SEG_C | SEG_B , | // O
93 | SEG_E | SEG_F | SEG_A | SEG_G , | // F
94 | SEG_E | SEG_F | SEG_A | SEG_G , | // F
95 | 0x00 ,
96 | };
97
98 | const uint8_t SEG_ALARM[] = {
99 | SEG_E | SEG_F | SEG_A | SEG_B | SEG_C | SEG_G , | // A
100 | SEG_F | SEG_E | SEG_D , | // L
101 | SEG_E | SEG_F | SEG_A | SEG_B | SEG_C | SEG_G , | // A
102 | 0x00 ,
103 | };
104
105 uint8_t PomVypis[] = { 0x00, 0x00, 0x00, 0x00 };
106
107 | //Hodnoty pro formátování displeje
108 | long BlikaniMil;
109 | bool StavBlikani = true;
110 | long OdpocetMil;
111 | bool OdpocetStav = true;
112
113 | // funkce pro vypnutí vnitřních hodin
114 | ISR (WDT_vect)
115 | {
116 | wdt_disable();
117 | }
118
119 | void setup() {
120 | // nastavení pinů jako výstupních
121 | pinMode(DIR_MIN, OUTPUT);
122 | pinMode(STEP_MIN, OUTPUT);

pinMode(DIR_HOD, OUTPUT);
pinMode(STEP_HOD, OUTPUT); pinMode(SLP_HOD, OUTPUT);
pinMode(SLP_MIN, OUTPUT);
pinMode(BUZZER, OUTPUT);

// připojení obou řídících pinů na zem digitalWrite(DIR_HOD, LOW); digitalWrite(STEP_HOD, LOW); digitalWrite(DIR_MIN, LOW); digitalWrite(STEP_MIN, LOW);

digitalWrite(SLP_HOD, LOW); digitalWrite(SLP_MIN, LOW);

// nastavení pinů jako vstupních pinMode(SET_TIME, INPUT_PULLUP); pinMode(UP_TIME, INPUT_PULLUP); pinMode(DOWN_TIME, INPUT_PULLUP); pinMode(KON_HOD, INPUT_PULLUP);
pinMode(KON_MIN, INPUT_PULLUP);

RTC.setClockMode(false); //nastavení 24 hodinového formátu času

//funkce pro hardwarové přerušení právě probíhajícího programu //na základě stisknutí tlačítka SET attachInterrupt(digitalPinToInterrupt(SET_TIME), Vzbudit, RISING);

//Nastavení výchozí polohy
HomeHod();
HomeMin();
}

void loop() {
Mode(); //kontrola stisku tlačítka SET

Debounce (); //funkce pro odstranění zákmitů u tlačítek

if (SetTimeMode == 0)
{
Synchronizace(); //funkce pro synchronizaci aktuálního času a polohy ciferníků
Alarm(); //funkce pro ověření spuštění alarmu

if (Hodiny == HodinyPol && Minuty == MinutyPol && AlarmStav == false)
{
enStiskSetTime == 1;
Uspat(); //přechod do režimu s nízkým odběrem proudu
}
}

else
{
NastaveniCasu(); //funkce pro nastavení času a alarmu
}

}

//ošetření zákmitu tlačítek
//pokud je stisk tlačítka zakázaný tak ho povol po uplynutí 200 milisekund void Debounce () {

if (enStiskSetTime == 0) {
if (millis() - stiskMilSetTime > 200) { enStiskSetTime = 1;
}
}

if (enStiskUpTime == 0) {
if (millis() - stiskMilUpTime > 200) { enStiskUpTime = 1;
}
}

if (enStiskDownTime == 0) {
if (millis() - stiskMilDownTime > 200) { enStiskDownTime = 1;
}
}
}

//stisk tlačítka SET
//nastavení prostředního tlačítka
// pokud je zvuková signalizace aktivní vypni ji, pokud ne nastav aktuální čas hodin
void Mode() {
stavTlacSetTime = digitalRead(SET_TIME);
if (stavTlacSetTime == LOW & enStiskSetTime == 1)
{
if (AlarmStav == true)
{
AlarmStav = false;
AlarmOvladani = false;
}

else
{
SetTimeMode = SetTimeMode + 1; OdpocetMil = millis();
}

stiskSetTime = HIGH;
}
if (stiskSetTime == HIGH) { stiskMilSetTime = millis(); enStiskSetTime = 0;
stiskSetTime = LOW;
}
}

//funkce pro nastavení aktuálního času void NastaveniCasu() {
//Načtení potřebných hodnot
if (SetTimeMode == 1)
{
Hodiny = RTC.getHour(h12, PM); Minuty = RTC.getMinute();
display.setBrightness(7, true); //display.setBrightness(0x0f); display.clear();
display.setSegments(SEG_SET); delay(1000);
SetTimeMode = 2;

245 | }
246 | //Nastavení hodin
247 | if (SetTimeMode == 2)
248 | {
249 | Blikani();
250 | UpHodiny();
251 | DownHodiny();
252 | Odpocet();
253 | }
254 | //Nastavení minut
255 | if (SetTimeMode == 3)
256 | {
257 | Blikani();
258 | UpMinuty();
259 | DownMinuty();
260 | Odpocet();
261 | }
262 | //Uložení hodnot do RTC modulu
263 | if (SetTimeMode == 4)
264 | {
265 | RTC.setHour(Hodiny);
266 | RTC.setMinute(Minuty);
267 | RTC.setClockMode(false);
268 | display.showNumberDecEx(RTC.getHour(h12, PM), 0b01000000, true, 2, 0);
269 | display.showNumberDecEx(RTC.getMinute(), 0b01000000, true, 2, 2);
270 | delay(1000);
271 | display.clear();
272 | display.setSegments(SEG_ALARM);
273 | Hodiny = HodinyAlarm;
274 | Minuty = MinutyAlarm;
275 | delay(1000);
276 | SetTimeMode = 5;
277 | }
278 | //Nastavení alarmu – hodiny
279 | if (SetTimeMode == 5)
280 | {
281 | Blikani();
282 | UpHodiny();
283 | DownHodiny();
284 | Odpocet();
285 | }
286 | //Nastavení alarmu – minuty
287 | if (SetTimeMode == 6)
288 | {
289 | Blikani();
290 | UpMinuty();
291 | DownMinuty();
292 | Odpocet();
293 | }
294 | //Nastavení alarmu – zapnutí
295 | if (SetTimeMode == 7)
296 | {
297 | if (AlarmOvladani == false)
298 | {
299 | display.setSegments(SEG_OFF);
300 | }
301 | if (AlarmOvladani == true)
302 | {
303 | display.setSegments(SEG_ON);
304 | }
305 | ToggleOnOff();

306 | Odpocet();
307 | }
308 | //Uložení nastavení alarmu
309 | if (SetTimeMode == 8)
310 | {
311 | HodinyAlarm = Hodiny;
312 | MinutyAlarm = Minuty;
313 | display.showNumberDecEx(HodinyAlarm, 0b01000000, true, 2, 0);
314 | display.showNumberDecEx(MinutyAlarm, 0b01000000, true, 2, 2);
315 | delay(2000);
316 | display.clear();
317 | SetTimeMode = 0;
318 | }
319 | }
320
321 | //zvyšuje nastavení hodinové hodnoty
322 | void UpHodiny() {
323 | stavTlacUpTime = digitalRead(UP_TIME);
324 | if (stavTlacUpTime == LOW & enStiskUpTime == 1)
325 | {
326 | Hodiny = Hodiny + 1;
327 | if (Hodiny > 23)
328 | {
329 | Hodiny = 0;
330 | }
331 | OdpocetMil = millis();
332 | stiskUpTime = HIGH;
333 | }
334 | if (stiskUpTime == HIGH) {
335 | stiskMilUpTime = millis();
336 | enStiskUpTime = 0;
337 | stiskUpTime = LOW;
338 | }
339 | }
340
341 | //snižuje nastavení hodinové hodnoty
342 | void DownHodiny() {
343 | stavTlacDownTime = digitalRead(DOWN_TIME);
344 | if (stavTlacDownTime == LOW & enStiskDownTime == 1)
345 | {
346 | Hodiny = Hodiny - 1;
347 | if (Hodiny < 0)
348 | {
349 | Hodiny = 23;
350 | }
351 | OdpocetMil = millis();
352 | stiskDownTime = HIGH;
353 | }
354 | if (stiskDownTime == HIGH) {
355 | stiskMilDownTime = millis();
356 | enStiskDownTime = 0;
357 | stiskDownTime = LOW;
358 | }
359 | }
360
361 | //zvyšuje nastavení minutové hodnoty
362 | void UpMinuty() {
363 | stavTlacUpTime = digitalRead(UP_TIME);
364 | if (stavTlacUpTime == LOW & enStiskUpTime == 1)
365 | {
366 | Minuty = Minuty + 1;

367 | if (Minuty > 59)
368 | {
369 | Minuty = 0;
370 | }
371 | OdpocetMil = millis();
372 | stiskUpTime = HIGH;
373 | }
374 | if (stiskUpTime == HIGH) {
375 | stiskMilUpTime = millis();
376 | enStiskUpTime = 0;
377 | stiskUpTime = LOW;
378 | }
379 | }
380
381 | //snižuje nastavení minutové hodnoty
382 | void DownMinuty() {
383 | stavTlacDownTime = digitalRead(DOWN_TIME);
384 | if (stavTlacDownTime == LOW & enStiskDownTime == 1)
385 | {
386 | Minuty = Minuty - 1;
387 | if (Minuty < 0)
388 | {
389 | Minuty = 59;
390 | }
391 | OdpocetMil = millis();
392 | stiskDownTime = HIGH;
393 | }
394 | if (stiskDownTime == HIGH) {
395 | stiskMilDownTime = millis();
396 | enStiskDownTime = 0;
397 | stiskDownTime = LOW;
398 | }
399 | }
400
401 | //přepíná mezi zapnutím a vypnutím alarmu
402 | void ToggleOnOff() {
403 | stavTlacDownTime = digitalRead(DOWN_TIME);
404 | if (stavTlacDownTime == LOW & enStiskDownTime == 1)
405 | {
406 | display.clear();
407 | AlarmOvladani = !AlarmOvladani;
408 | OdpocetMil = millis();
409 | stiskDownTime = HIGH;
410 | }
411 | if (stiskDownTime == HIGH) {
412 | stiskMilDownTime = millis();
413 | enStiskDownTime = 0;
414 | stiskDownTime = LOW;
415 | }
416
417 | stavTlacUpTime = digitalRead(UP_TIME);
418 | if (stavTlacUpTime == LOW & enStiskUpTime == 1)
419 | {
420 | display.clear();
421 | AlarmOvladani = !AlarmOvladani;
422 | OdpocetMil = millis();
423 | stiskUpTime = HIGH;
424 | }
425 | if (stiskUpTime == HIGH) {
426 | stiskMilUpTime = millis();
427 | enStiskUpTime = 0;

stiskUpTime = LOW;
}
}

//nastavení výchozí polohy hodinového ciferníku void HomeHod() {
digitalWrite(DIR_HOD, LOW); digitalWrite(SLP_HOD, HIGH);

while (1)
{
stavTlacKonHod = digitalRead(KON_HOD);

if (stavTlacKonHod == LOW)
{
HodinyPol = 0;
digitalWrite(SLP_HOD, LOW); break;
}
digitalWrite(STEP_HOD, HIGH); delayMicroseconds(Rychlost); digitalWrite(STEP_HOD, LOW); delayMicroseconds(Rychlost);
}
}

//nastavení výchozí polohy minutového ciferníku void HomeMin() {
digitalWrite(DIR_MIN, HIGH); digitalWrite(SLP_MIN, HIGH);

while (1)
{
stavTlacKonMin = digitalRead(KON_MIN);

if (stavTlacKonMin == LOW)
{
MinutyPol = 0;
digitalWrite(SLP_MIN, LOW); break;
}

digitalWrite(STEP_MIN, HIGH); delayMicroseconds(Rychlost); digitalWrite(STEP_MIN, LOW); delayMicroseconds(Rychlost);
}
}

//zajišťuje synchronizaci aktuálního a zobrazovaného času void Synchronizace() {
Hodiny = RTC.getHour(h12, PM);
Minuty = RTC.getMinute();

if (Hodiny > 12)
{
Hodiny = RTC.getHour(h12, PM) - 12;
}

if (Hodiny > HodinyPol)
{

489 | digitalWrite(DIR_HOD, HIGH);
490 | digitalWrite(SLP_HOD, HIGH);
491 | delay(1);
492 | while (Hodiny > HodinyPol)
493 | {
494 | HodPosun();
495 | }
496 | digitalWrite(SLP_HOD, LOW);
497 | }
498
499 | if (Minuty > MinutyPol)
500 | {
501 | digitalWrite(DIR_MIN, LOW);
502 | digitalWrite(SLP_MIN, HIGH);
503 | delay(1);
504 | while (Minuty > MinutyPol)
505 | {
506 | MinPosun();
507 | }
508 | digitalWrite(SLP_MIN, LOW);
509 | }
510
511 | if (Hodiny < HodinyPol)
512 | {
513 | HomeHod();
514 | }
515
516 | if (Minuty < MinutyPol)
517 | {
518 | HomeMin();
519 | }
520 | }
521
522 | //posun o 1 minutu
523 | void MinPosun() {
524 | for (int i = 0; i <= KrokyMin; i++)
525 | {
526 | digitalWrite(STEP_MIN, HIGH);
527 | delayMicroseconds(Rychlost);
528 | digitalWrite(STEP_MIN, LOW);
529 | delayMicroseconds(Rychlost);
530 | }
531 | MinutyPol = MinutyPol + 1;
532 | }
533
534 | //posun o 1 hodinu
535 | void HodPosun() {
536 | for (int i = 0; i <= KrokyHod; i++)
537 | {
538 | digitalWrite(STEP_HOD, HIGH);
539 | delayMicroseconds(Rychlost);
540 | digitalWrite(STEP_HOD, LOW);
541 | delayMicroseconds(Rychlost);
542 | }
543 | HodinyPol = HodinyPol + 1;
544 | }
545
546 | //Mód šetření energií
547 | void Uspat() {
548 | digitalWrite(DIR_HOD, LOW);
549 | digitalWrite(STEP_HOD, LOW);

digitalWrite(DIR_MIN, LOW); digitalWrite(STEP_MIN, LOW); digitalWrite(SLP_HOD, LOW); digitalWrite(SLP_MIN, LOW); display.clear();
// vypne ADC
ADCSRA = 0;
// clear various "reset" flags MCUSR = 0;
// allow changes, disable reset
WDTCSR = bit (WDCE) | bit (WDE);
// Nastavení přerušení a časový interval
562 | WDTCSR = bit (WDIE) | bit (WDP3) | bit (WDP0); | // nastav WDIE, a 8
| sekundový delay
| wdt_reset();
| set_sleep_mode (SLEEP_MODE_PWR_DOWN);
| noInterrupts ();
| sleep_enable();
| attachInterrupt (0, Vzbudit, FALLING);
| EIFR = bit (INTF0);
| MCUCR = bit (BODS) | bit (BODSE);
| MCUCR = bit (BODS);
| interrupts ();
| sleep_cpu ();
| sleep_disable();
}
| // vypnout mód pro šetření energií
| void Vzbudit()
{
| sleep_disable();
| detachInterrupt (0);
}

//podprogram zajišťující problikávání právně nastavované hodnoty na
| displeji
| void Blikani() {
| if (StavBlikani)
{
| BlikaniMil = millis();
| StavBlikani = false;
}
| if ((millis() - BlikaniMil) < 500)
{
| if (SetTimeMode == 2 || SetTimeMode == 5)
{
| PomVypis[0] = 0x00;
| PomVypis[1] = 0x00;
PomVypis[2] = display.encodeDigit(Minuty / 10); PomVypis[3] = display.encodeDigit(Minuty % 10);
| display.setSegments(PomVypis);
}
| if (SetTimeMode == 3 || SetTimeMode == 6)
{
PomVypis[0] = display.encodeDigit(Hodiny / 10); PomVypis[1] = display.encodeDigit(Hodiny % 10);
| PomVypis[2] = 0x00;
| PomVypis[3] = 0x00;
| display.setSegments(PomVypis);

}
}
if ((millis() - BlikaniMil) > 500)
{
display.showNumberDecEx(Hodiny, 0b01000000, true, 2, 0); display.showNumberDecEx(Minuty, 0b01000000, true, 2, 2);

if ((millis() - BlikaniMil) > 1000)
{
StavBlikani = true;
}
}
}

//vypne režim pro nastavení aktuálního času při absenci vstupu, která trvá déle než jednu minutu
void Odpocet() {
if ((millis() - OdpocetMil) > 60000)
{
if (SetTimeMode < 4)
{
RTC.setHour(Hodiny);
RTC.setMinute(Minuty);
RTC.setClockMode(false);
Hodiny = RTC.getHour(h12, PM);
Minuty = RTC.getMinute();
display.showNumberDecEx(Hodiny, 0b01000000, true, 2, 0); display.showNumberDecEx(Minuty, 0b01000000, true, 2, 2); delay(1000);
display.clear();
SetTimeMode = 0;
}
else
{
SetTimeMode = 8;
}
}
}

//funkce alarmu
//pokud je alarm aktivní srovnej aktuální a nastavený čas pro alarm, pokud jsou shodné zapni zvukovou signalizaci
void Alarm() {
if (RTC.getHour(h12, PM) == HodinyAlarm && RTC.getMinute() == MinutyAlarm && AlarmOvladani == true)
{
AlarmStav = true;
}

if (AlarmStav == true)
{
for (int i = 0; i <= 3; i++)
{
tone(BUZZER, 500);
delay(50);
noTone(BUZZER);
delay(50);
}
delay(1000);
}
}

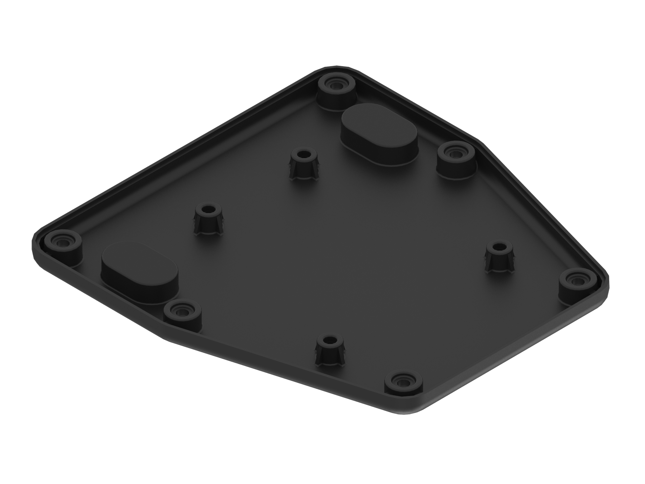
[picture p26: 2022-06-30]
Renderované snímky/zadní díl.3.png

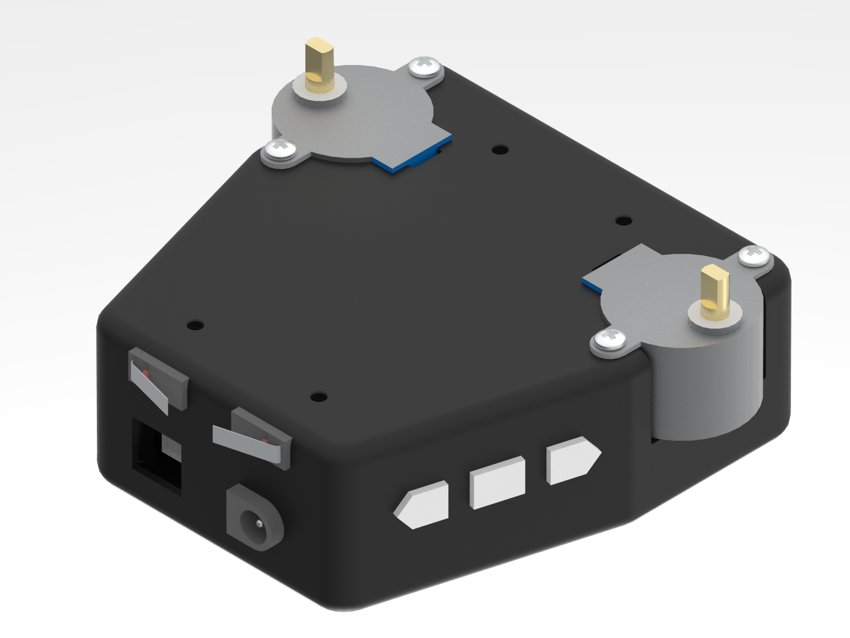
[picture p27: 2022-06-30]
Renderované snímky/sestava.14.png

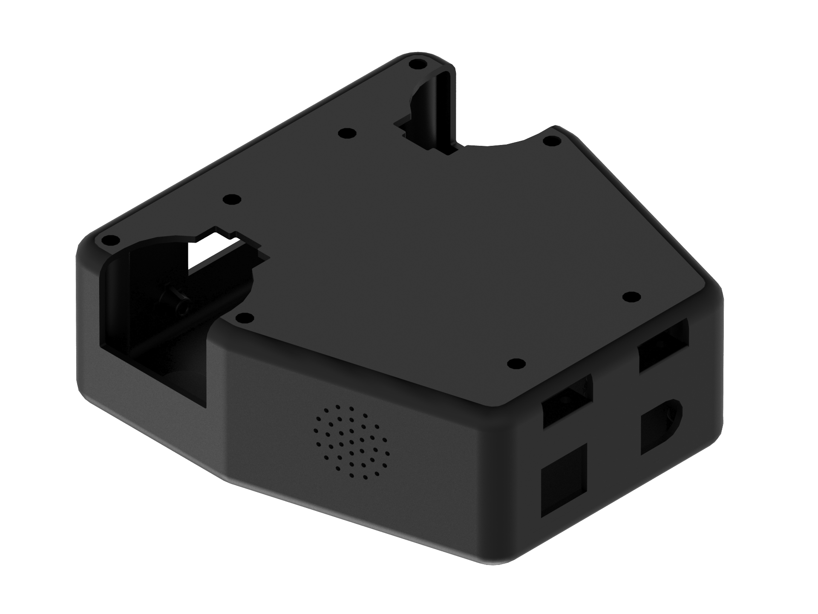
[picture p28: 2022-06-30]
Renderované snímky/kryt.jpg

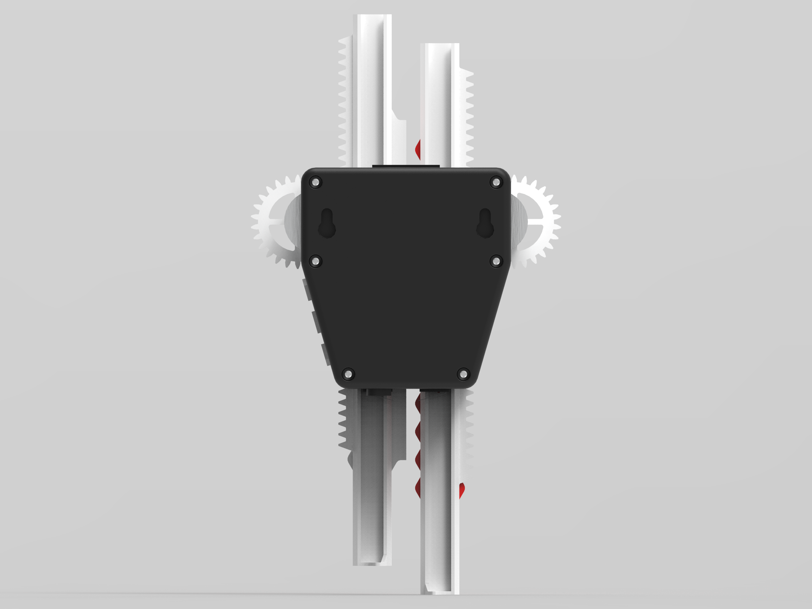
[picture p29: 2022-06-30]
Renderované snímky/lineární hodiny.25.png

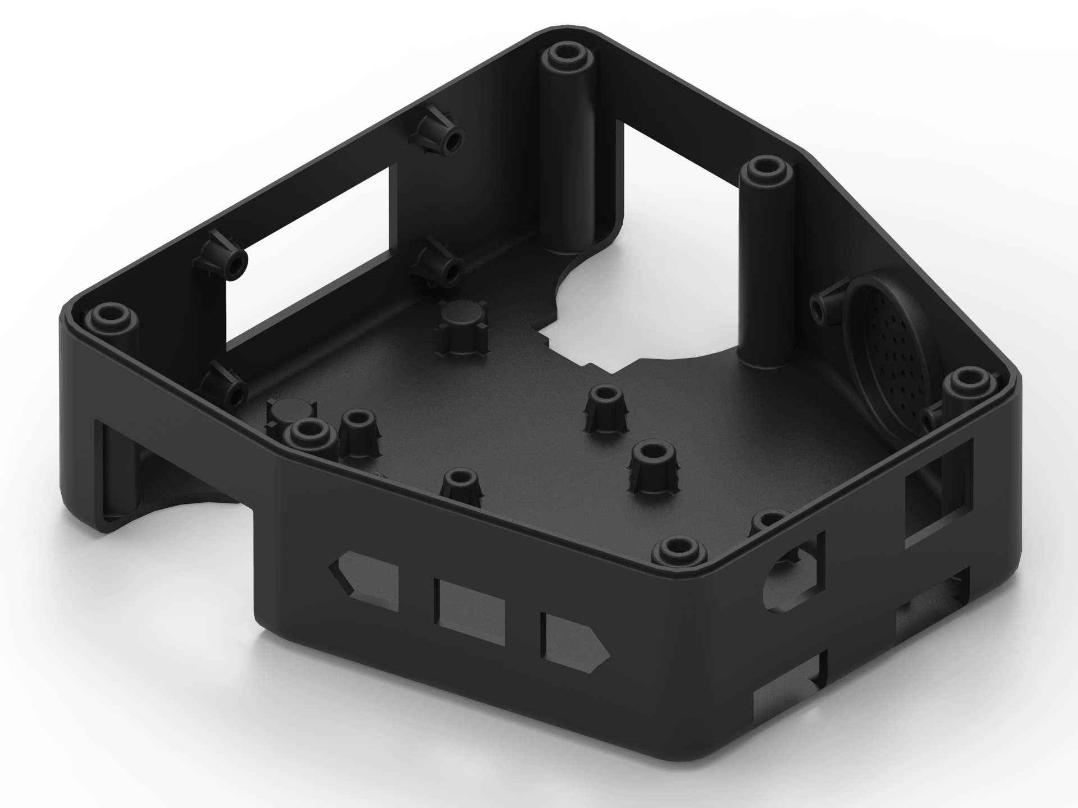
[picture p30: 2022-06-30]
Renderované snímky/čelní díl.png

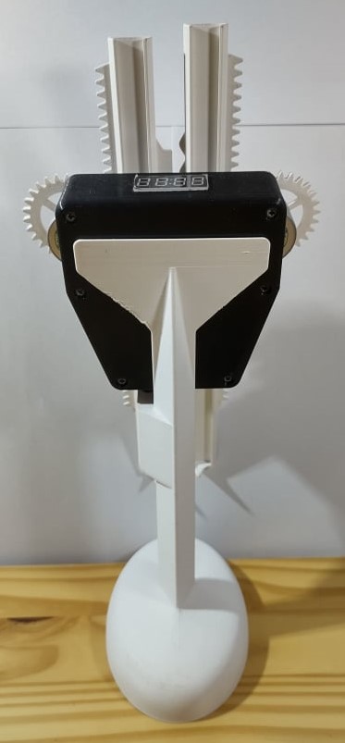
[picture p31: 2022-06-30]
Fotografie/Lineární hodiny9.jpg

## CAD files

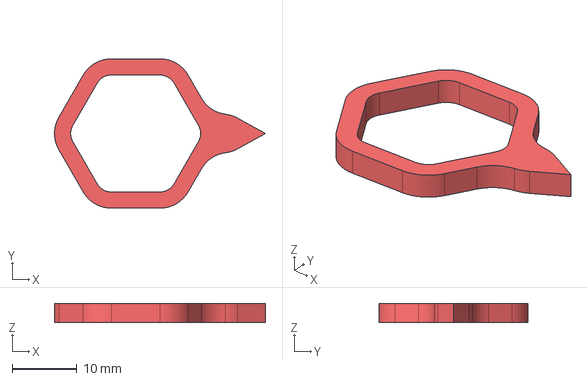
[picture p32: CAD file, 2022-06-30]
Modely dílů/STEP/Rucicka.stp
32.5 x 23.0 x 3.00 mm

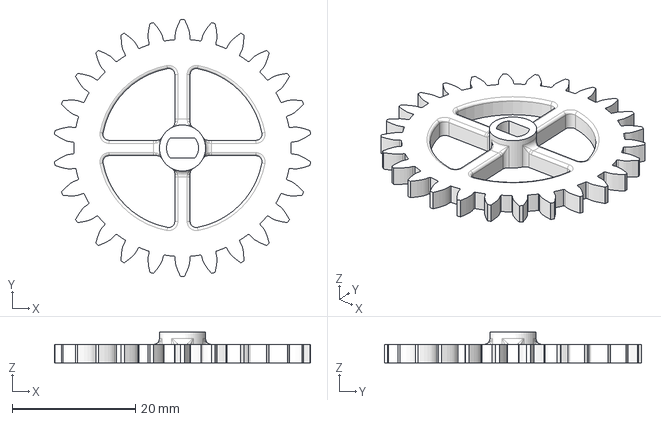
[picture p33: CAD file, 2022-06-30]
Modely dílů/STEP/Pastorek.stp
41.6 x 41.8 x 5.00 mm

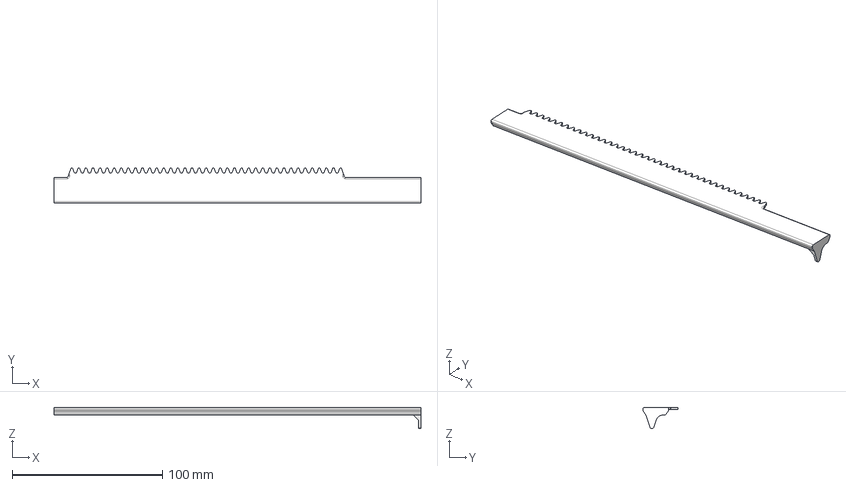
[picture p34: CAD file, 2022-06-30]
Modely dílů/STEP/OzubenyHrebenMinutovy.stp
244.5 x 23.6 x 14.0 mm

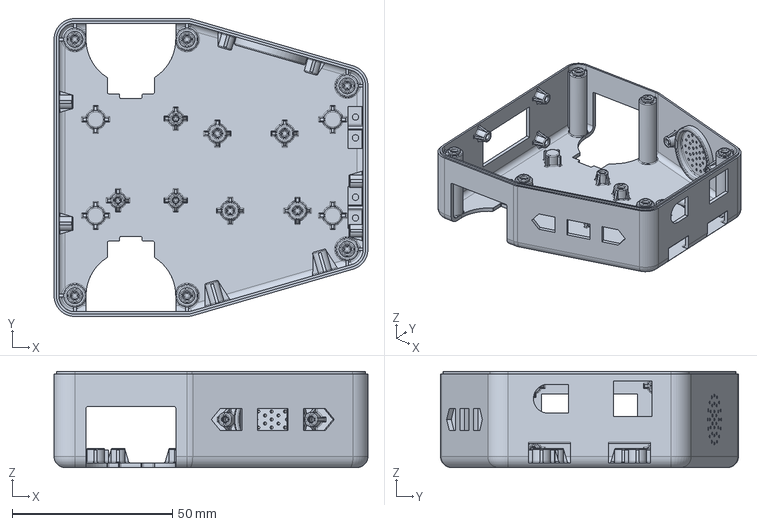
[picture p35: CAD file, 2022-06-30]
Modely dílů/STEP/CelniKryt.stp
98.0 x 93.0 x 30.0 mm

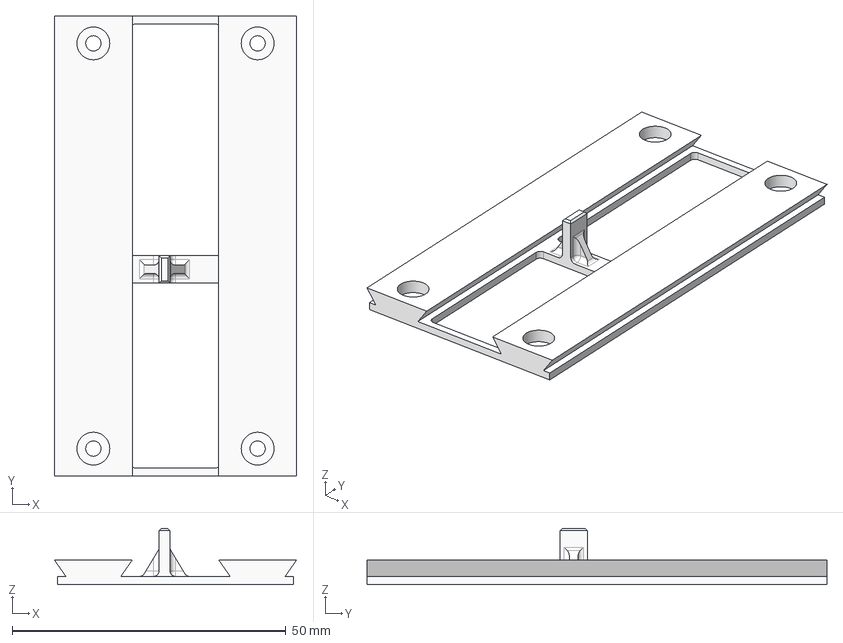
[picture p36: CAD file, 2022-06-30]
Modely dílů/STEP/kolejnice.stp
44.2 x 84.0 x 10.2 mm

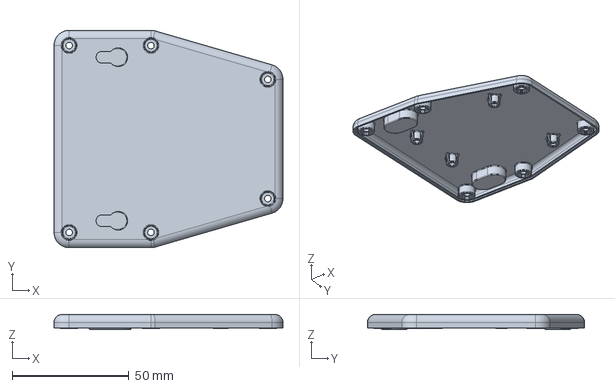
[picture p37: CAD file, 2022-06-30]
Modely dílů/STEP/ZadniKryt.stp
98.0 x 93.0 x 6.50 mm

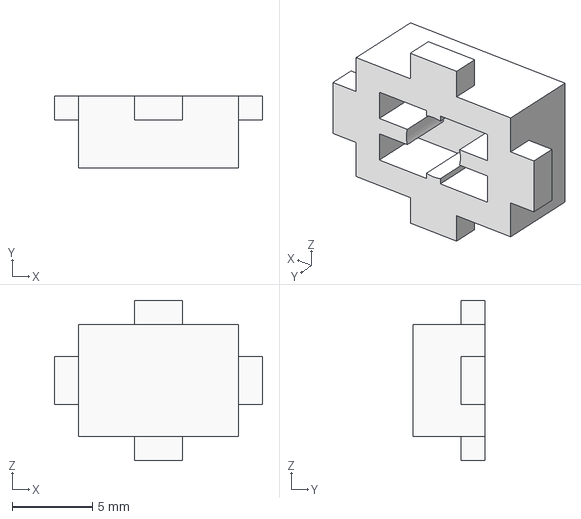
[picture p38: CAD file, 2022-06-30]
Modely dílů/STEP/HmatnikSET.stp
13.0 x 4.50 x 10.0 mm

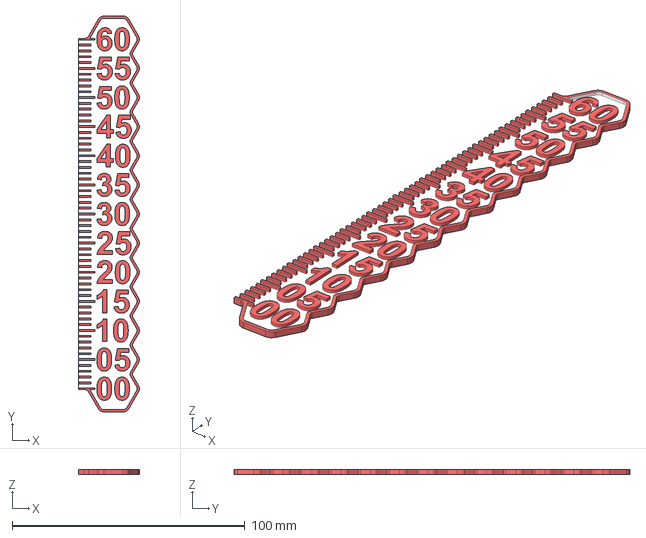
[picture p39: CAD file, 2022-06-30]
Modely dílů/STEP/CifernikMinutovy .stp
26.1 x 170.0 x 2.00 mm

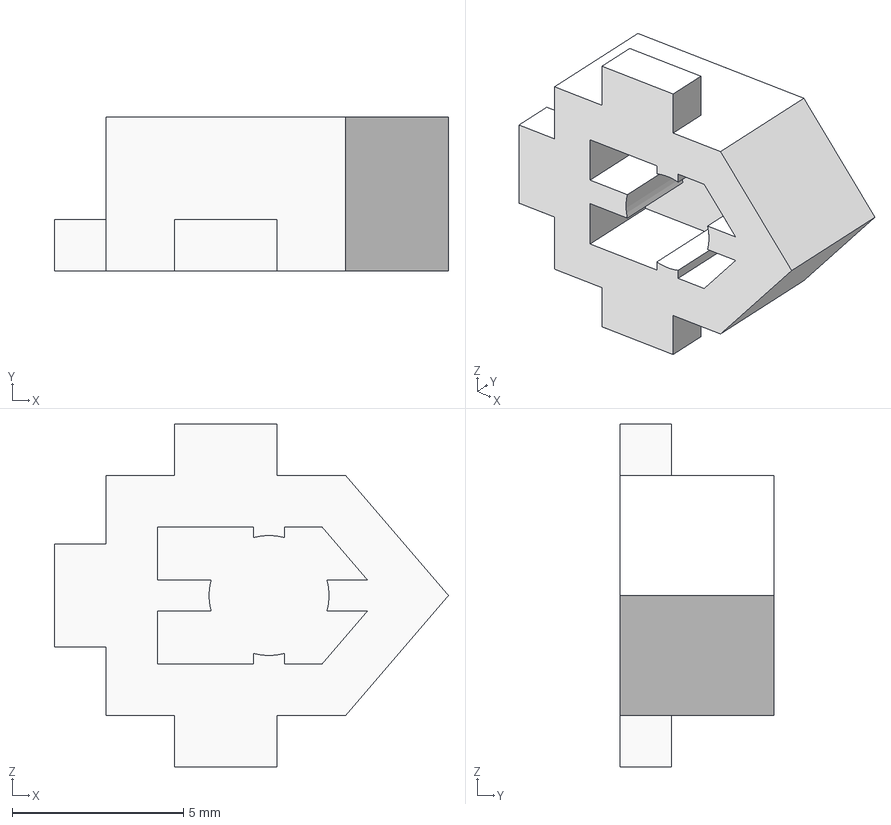
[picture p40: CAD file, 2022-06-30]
Modely dílů/STEP/HmatnikSipka.stp
11.5 x 4.50 x 10.0 mm

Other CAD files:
Modely dílů/STEP/OzubenyHrebenHodinovy.stp

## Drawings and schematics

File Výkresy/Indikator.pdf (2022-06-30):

( ) 32,81

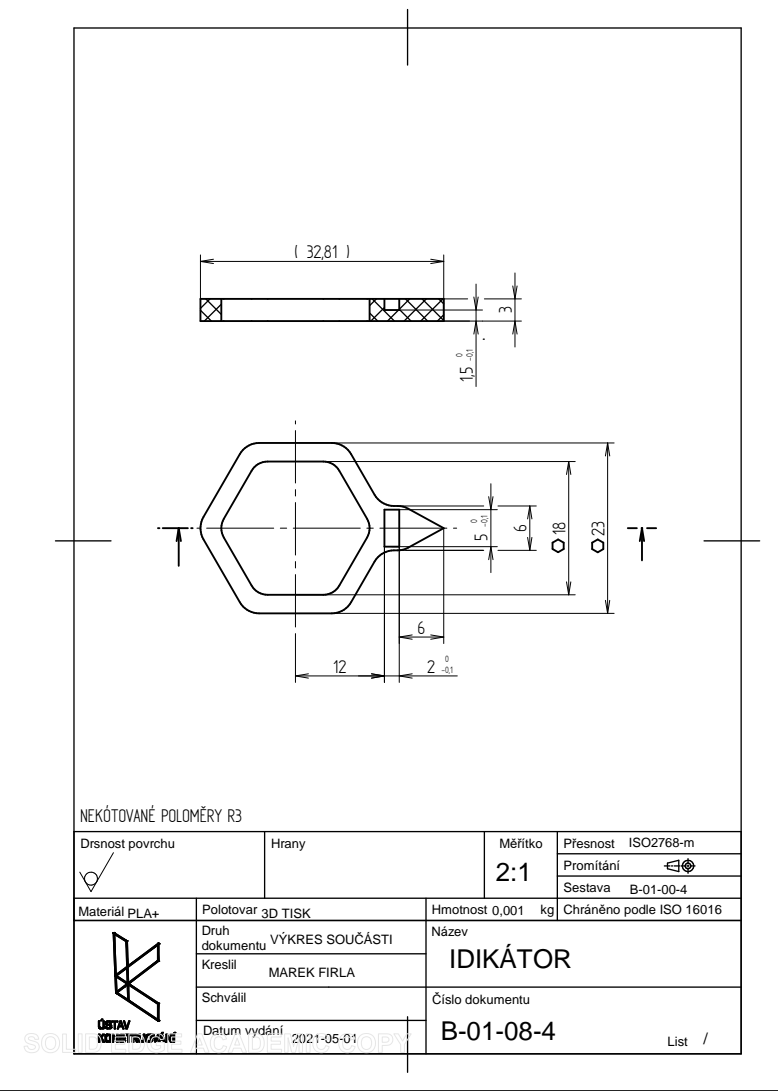
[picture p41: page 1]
MAREK FIRLA; Kreslil; Drsnost povrchu; Hrany; Měřítko; Promítání; Přesnost; Sestava; NEKÓTOVANÉ POLOMĚRY R3; ISO2768-m

Materiál PLA+ | Polotovar 3D TISK | Hmotnost 0,001 kg | Chráněno podle ISO 16016

Druh VÝKRES SOUČÁSTI dokumentu | Název IDIKÁTOR

Schválil | Číslo dokumentu B-01-08-4 List /

Datum vydání

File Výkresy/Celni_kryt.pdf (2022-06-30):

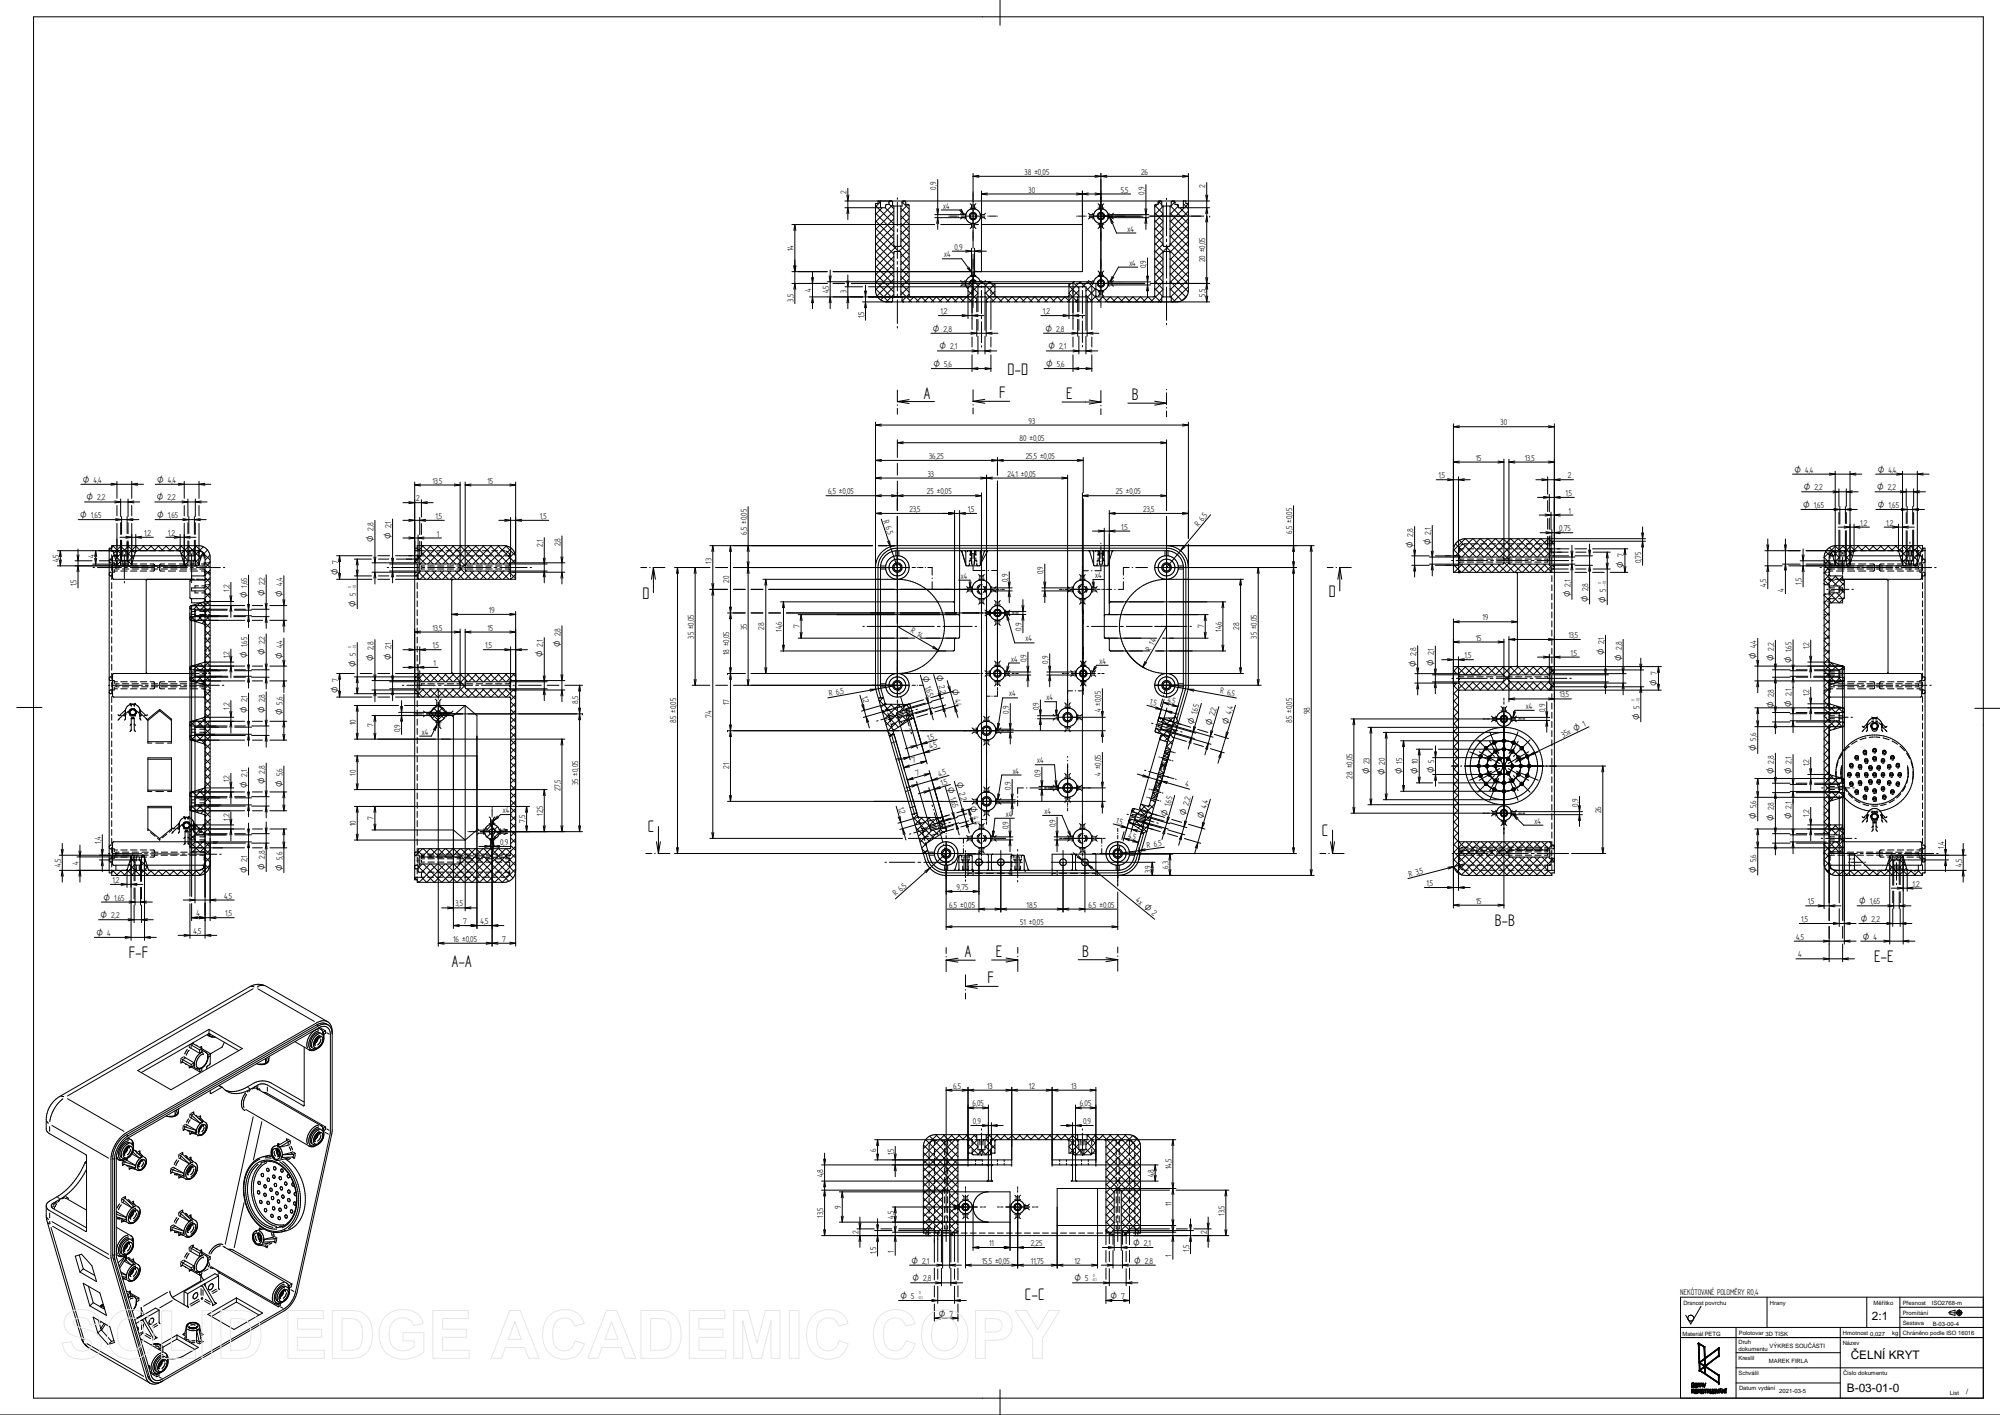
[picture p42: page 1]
MAREK FIRLA; VÝKRES SOU; ČÁSTI; ČELNÍ KRYT; PETG; 3D TISK; Datum vydání; Kreslil; Schválil; Číslo dokumentu; Drsnost povrchu; Materiál; Polotovar; dokumentu; Druh; Název; Hmotnost; Hrany; Měřítko; Přesnost; List; Sestava; NEKÓTOVANÉ POLOMĚRY R0,4; ISO2768-m

Promítání
ěno podle ISO 16016
Chrán

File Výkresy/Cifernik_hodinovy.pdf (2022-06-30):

1

2

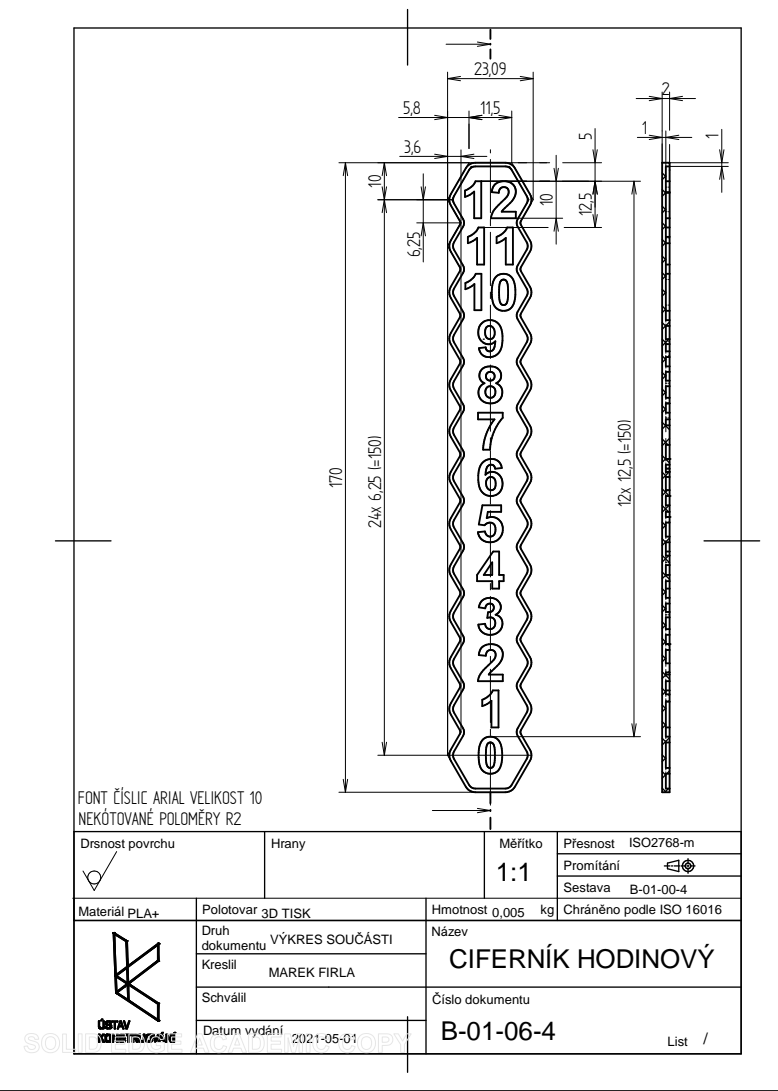
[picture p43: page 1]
MAREK FIRLA; Kreslil; Drsnost povrchu; Hrany; Měřítko; Promítání; Přesnost; Sestava; ISO2768-m

FONT ČÍSLIC ARIAL VELIKOST 10
NEKÓTOVANÉ POLOMĚRY R2

Materiál PLA+ | Polotovar 3D TISK | Hmotnost kg 0,005 | Chráněno podle ISO 16016

Druh VÝKRES SOUČÁSTI dokumentu | Název CIFERNÍK HODINOVÝ

Schválil | Číslo dokumentu B-01-06-4 List /

Datum vydání 2021-05-01

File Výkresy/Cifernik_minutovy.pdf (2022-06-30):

7

5

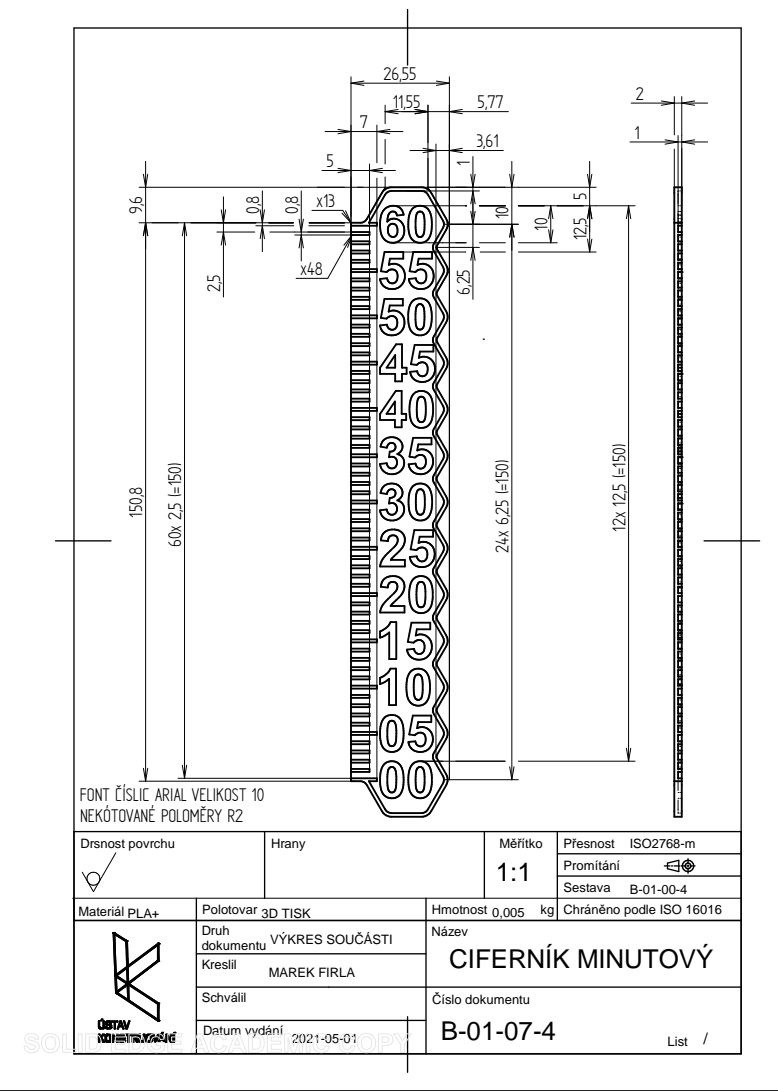
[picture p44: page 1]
MAREK FIRLA; Kreslil; Drsnost povrchu; Hrany; Měřítko; Promítání; Přesnost; Sestava; ISO2768-m

FONT ČÍSLIC ARIAL VELIKOST 10
NEKÓTOVANÉ POLOMĚRY R2

Materiál PLA+ | Polotovar 3D TISK | Hmotnost kg 0,005 | Chráněno podle ISO 16016

Druh VÝKRES SOUČÁSTI dokumentu | Název CIFERNÍK MINUTOVÝ

Schválil | Číslo dokumentu B-01-07-4 List /

Datum vydání 2021-05-01

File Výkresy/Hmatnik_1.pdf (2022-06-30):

13
10 0

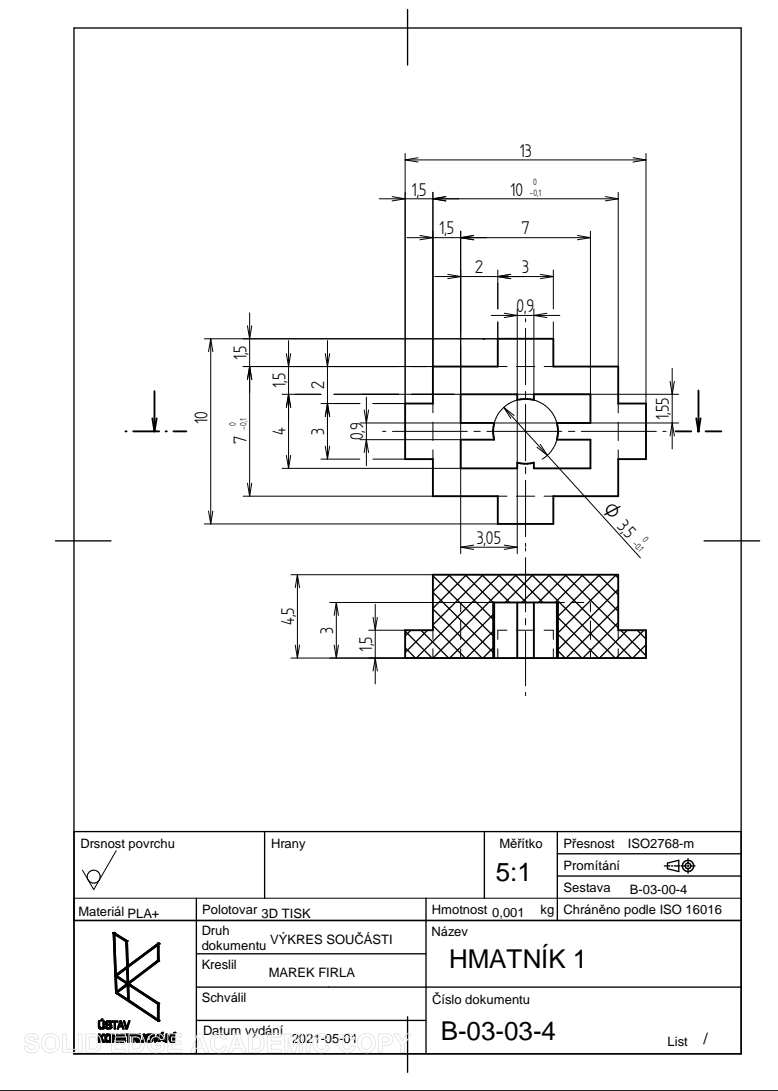
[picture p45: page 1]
MAREK FIRLA; Kreslil; Drsnost povrchu; Hrany; Měřítko; Promítání; Přesnost; Sestava; ISO2768-m

1,5 7
2 3

Materiál PLA+ | Polotovar 3D TISK | Hmotnost kg 0,001 | Chráněno podle ISO 16016

Druh VÝKRES SOUČÁSTI dokumentu | Název HMATNÍK 1

Schválil | Číslo dokumentu B-03-03-4 List /

Datum vydání

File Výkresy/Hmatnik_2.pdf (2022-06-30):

7 0

2 3

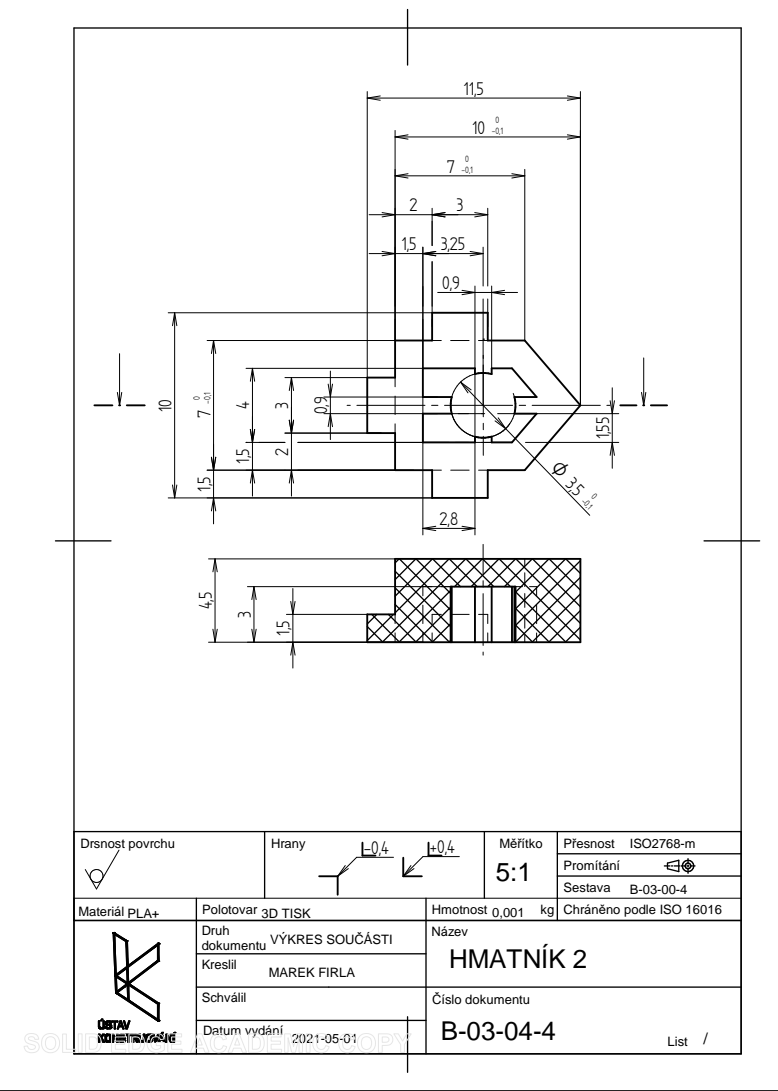
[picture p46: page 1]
MAREK FIRLA; Kreslil; Drsnost povrchu; Hrany; Měřítko; Promítání; Přesnost; Sestava; ISO2768-m

Materiál PLA+ | Polotovar 3D TISK | Hmotnost kg 0,001 | Chráněno podle ISO 16016

Druh VÝKRES SOUČÁSTI dokumentu | Název HMATNÍK 2

Schválil | Číslo dokumentu B-03-04-4 List /

Datum vydání

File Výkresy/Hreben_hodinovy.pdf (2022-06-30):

1,5

3,5

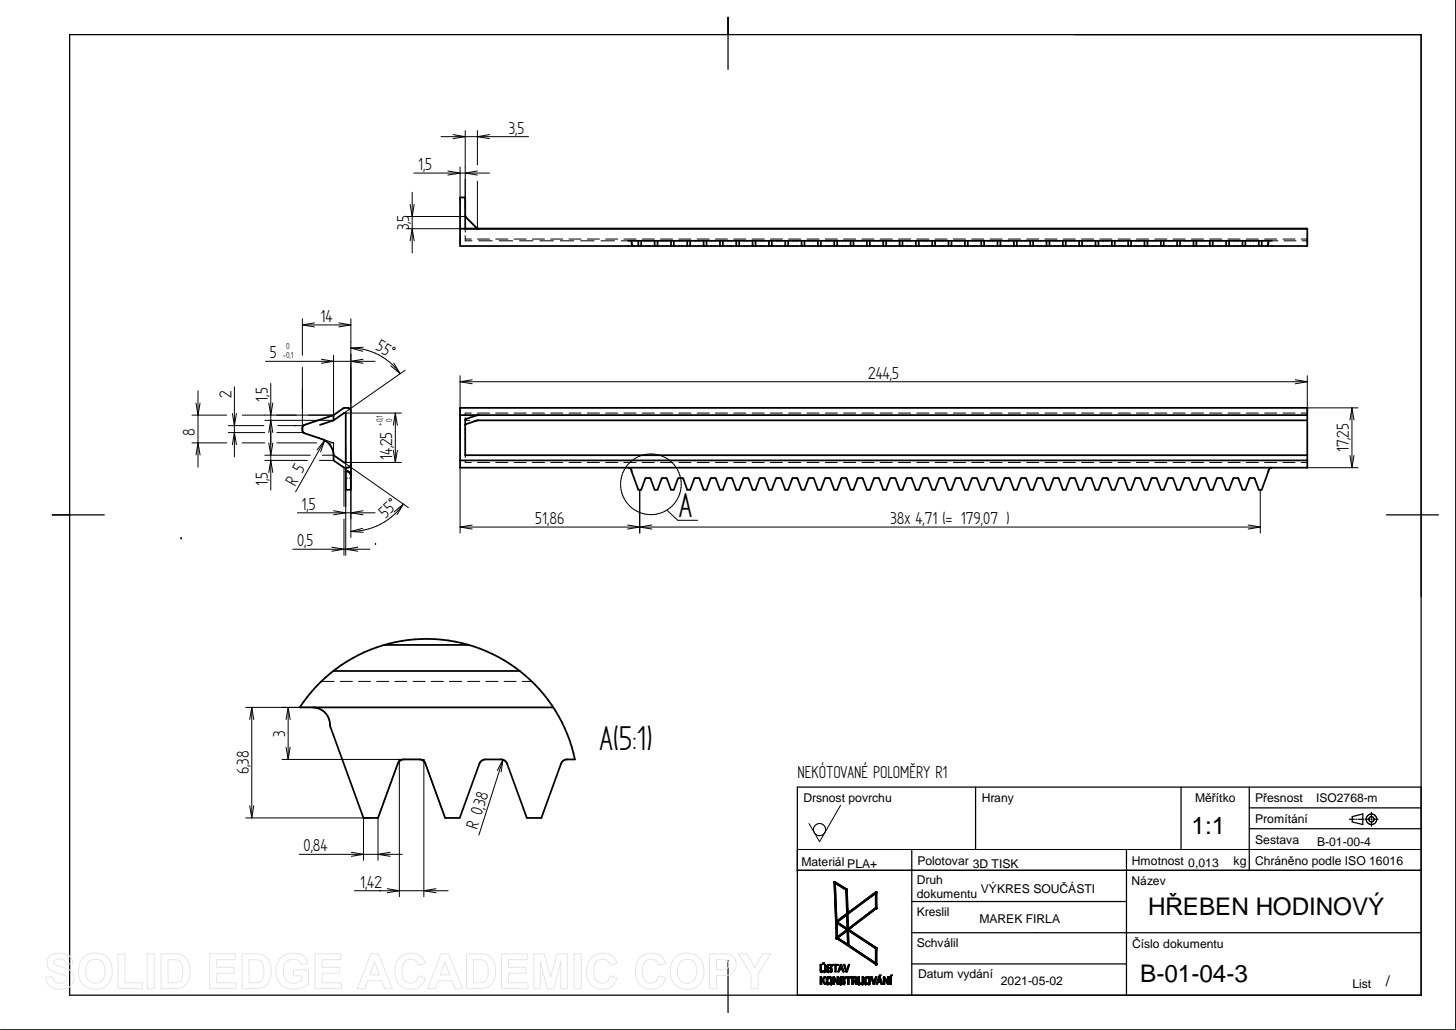
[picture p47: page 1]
MAREK FIRLA; Datum vydání; Kreslil; Schválil; Číslo dokumentu; Drsnost povrchu; Hrany; Měřítko; Přesnost; List; Sestava; ISO2768-m; NEKÓTOVANÉ POLOMĚRY R1

Promítání
Chráněno podle ISO 16016

Materiál PLA+ | Polotovar 3D TISK | Hmotnost kg 0,013

Druh VÝKRES SOUČÁSTI dokumentu | Název HŘEBEN HODINOVÝ

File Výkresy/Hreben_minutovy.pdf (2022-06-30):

3,5

1,5

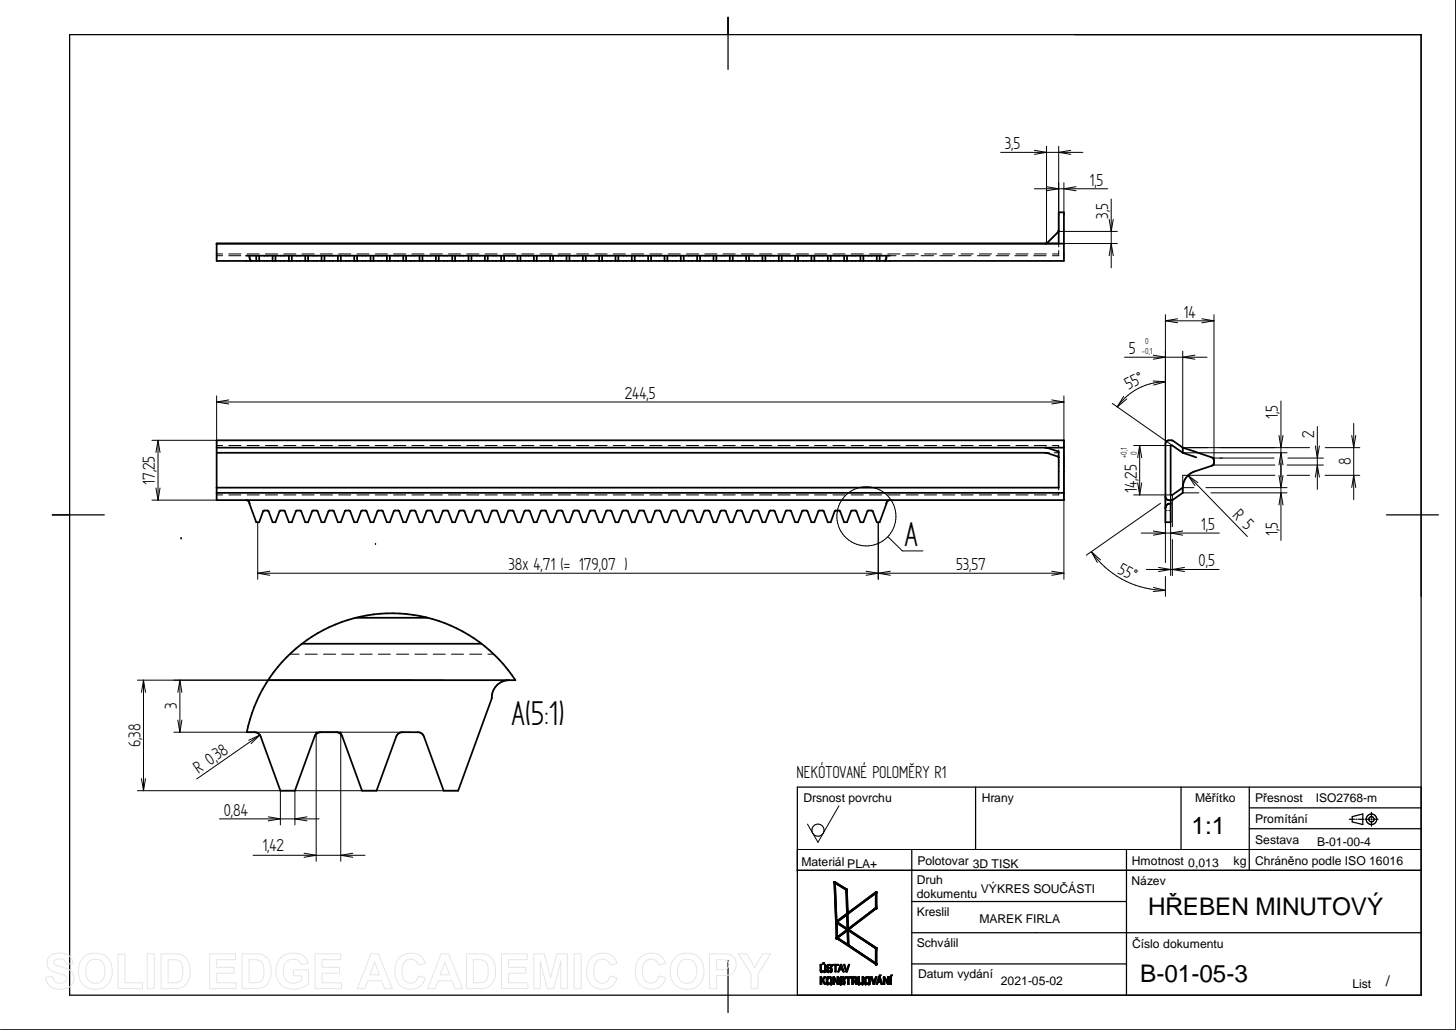
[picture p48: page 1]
MAREK FIRLA; Datum vydání; Kreslil; Schválil; Číslo dokumentu; Drsnost povrchu; Hrany; Měřítko; Přesnost; List; Sestava; ISO2768-m; R 0,38 NEKÓTOVANÉ POLOMĚRY R1

Promítání
Chráněno podle ISO 16016

Materiál PLA+ | Polotovar 3D TISK | Hmotnost kg 0,013

Druh VÝKRES SOUČÁSTI dokumentu | Název HŘEBEN MINUTOVÝ

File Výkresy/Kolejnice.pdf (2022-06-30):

2

12 | 3

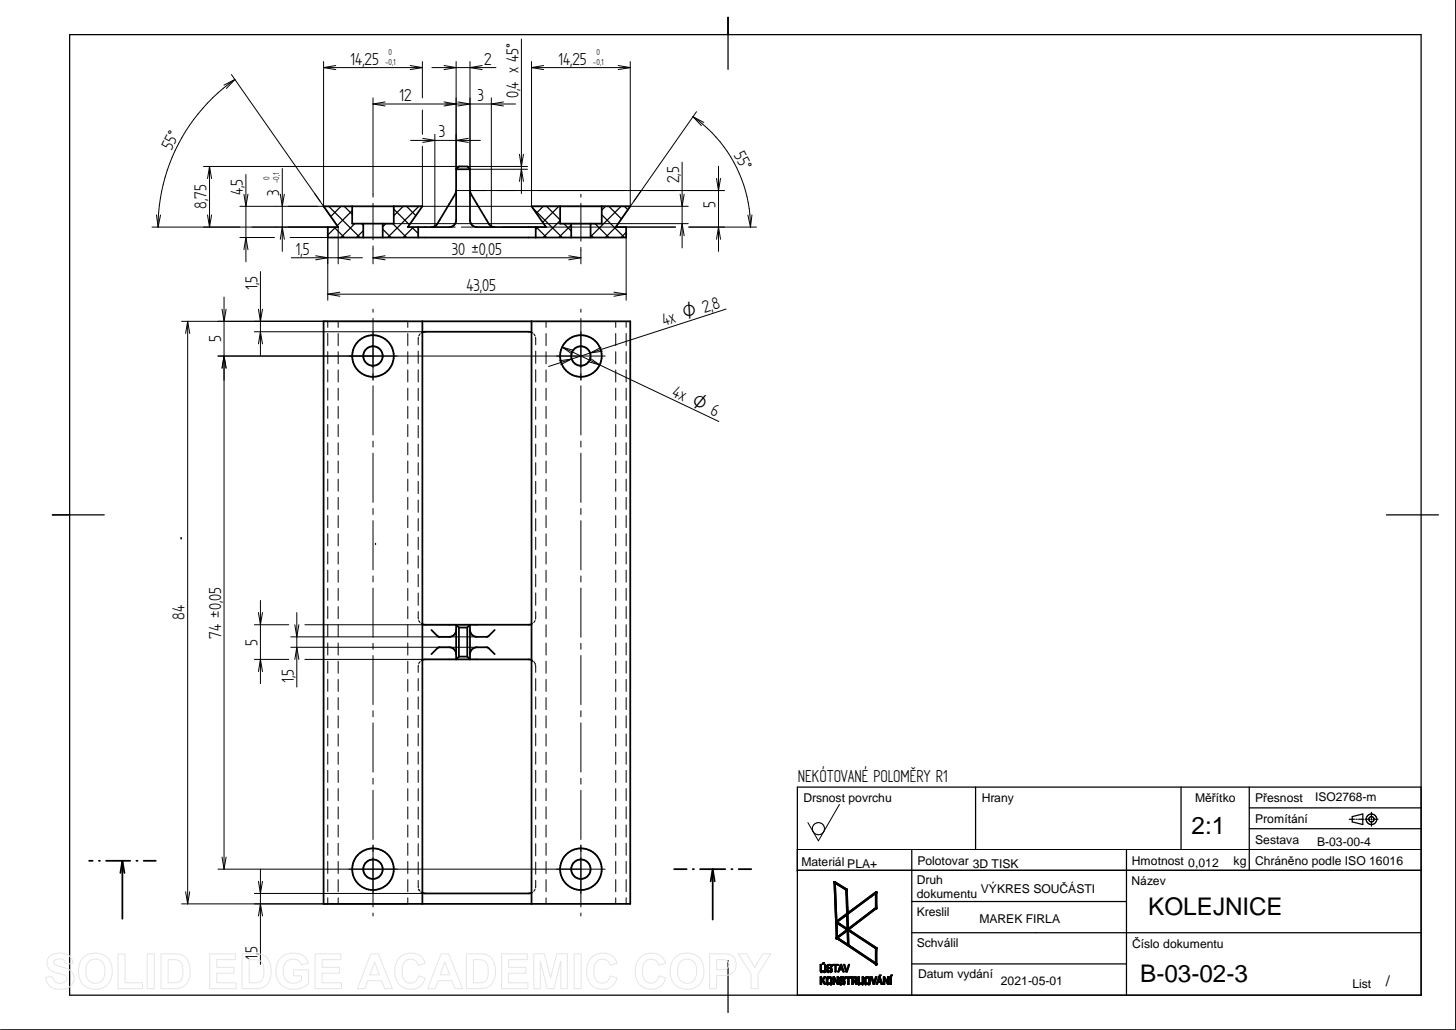
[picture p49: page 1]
MAREK FIRLA; Datum vydání; Kreslil; Schválil; Číslo dokumentu; Drsnost povrchu; Hrany; Měřítko; Promítání; Přesnost; List; Sestava; NEKÓTOVANÉ POLOMĚRY R1; ISO2768-m

Materiál PLA+ | Polotovar 3D TISK | Hmotnost kg 0,012 | Chráněno podle ISO 16016

Druh VÝKRES SOUČÁSTI dokumentu | Název KOLEJNICE

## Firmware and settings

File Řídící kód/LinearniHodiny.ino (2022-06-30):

//Lineární hodiny
//Marek Firla

// připojení potřebných knihoven
//#include <Arduino.h> //knihovny použité při ladění programu
//#include <Wire.h>
#include <DS3231.h> //knihovna zajišťující funkci modulu reálného času
#include <TM1637Display.h> //knihovna pro ovládání displeje
#include <avr/sleep.h> //knihovny pro uspání Arduina
#include <avr/wdt.h>

// nastavení čísel propojovacích pinů
#define SLP_HOD 0
#define SLP_MIN 1
#define DOWN_TIME 2
#define SET_TIME 3
#define UP_TIME 4
#define CLK 5
#define DIO 6
#define DIR_HOD 7
#define STEP_HOD 8
#define DIR_MIN 9
#define STEP_MIN 10
#define KON_HOD 11
#define KON_MIN 12
#define BUZZER 13

TM1637Display display(CLK, DIO); // vytvoření instance displej z knihovny TM1637
DS3231 RTC; // inicializace RTC z knihovny

//deklarace proměnných
int Hodiny; // proměnná uchovávající aktuální Hodinu
int Minuty; // proměnná uchovávající aktuální minutu
bool h12; // logická proměnná pro nastavení 24 nebo 12 hodinového formátu
bool PM;  // logické proměnná pro rozlišení dopolední a odpoledního času
int HodinyPol; // proměnná uchovávající aktuální polohu hodinového ciferníku vůči indikátoru
int MinutyPol; // proměnná uchovávající aktuální polohu hodinového ciferníku vůči indikátoru
int HodinyAlarm; // proměnná uchovávající čas alarmu
int MinutyAlarm;
bool AlarmOvladani = false; //logická proměnná pro zapnutí nebo vypnutí alarmu
bool AlarmStav = false; //logická proměnná indikující stav zvukové signalizace

// proměnné sloužící pro ošetření zákmitů tlačítek
int enStiskSetTime = 1;      // proměnná povolení stisku
long stiskMilSetTime = 0;    // proměnná pro čas stisku
int stiskSetTime = LOW;      // proměnná pro kontrolu stisku
int stavTlacSetTime = 0;     // proměnná stavu tlačítka

int enStiskUpTime = 1;      // proměnná povolení stisku
long stiskMilUpTime = 0;    // proměnná pro čas stisku
int stiskUpTime = LOW;      // proměnná pro kontrolu stisku
int stavTlacUpTime = 0;     // proměnná stavu tlačítka

int enStiskDownTime = 1;      // proměnná povolení stisku
long stiskMilDownTime = 0;    // proměnná pro čas stisku
int stiskDownTime = LOW;      // proměnná pro kontrolu stisku
int stavTlacDownTime = 0;     // proměnná stavu tlačítka

int stavTlacKonHod = 0;       // proměnná stavu tlačítka
int stavTlacKonMin = 0;       // proměnná stavu tlačítka

int KrokyMin = 334;  //proměnná pro počet kroků motoru pro lineární posun o rozestup jednotlivých označení minut na ciferníku
int KrokyHod = 1672; //proměnná pro počet kroků motoru pro lineární posun o rozestup jednotlivých označení hodin na ciferníku

int Rychlost = 122; //přepočet na délku mezery mezi impulzy

int SetTimeMode = 0; //proměnná pro přepínání módů nastavení hodin

//hodnoty pro informativní nápisy na displeji
const uint8_t SEG_SET[] = {
  SEG_A | SEG_F | SEG_G | SEG_C | SEG_D ,           // S
  SEG_A | SEG_F | SEG_G | SEG_E | SEG_D ,           // E
  SEG_F | SEG_G | SEG_E | SEG_D ,                   // T
  0x00 ,
};

const uint8_t SEG_ON[] = {
  SEG_A | SEG_F | SEG_E | SEG_D | SEG_C | SEG_B ,   // O
  SEG_E | SEG_G | SEG_C | SEG_E ,                   // N
  0x00 ,
  0x00 ,
};

const uint8_t SEG_OFF[] = {
  SEG_A | SEG_F | SEG_E | SEG_D | SEG_C | SEG_B ,    // O
  SEG_E | SEG_F | SEG_A | SEG_G ,                   // F
  SEG_E | SEG_F | SEG_A | SEG_G ,                   // F
  0x00 ,
};

const uint8_t SEG_ALARM[] = {
  SEG_E | SEG_F | SEG_A | SEG_B | SEG_C | SEG_G ,   // A
  SEG_F | SEG_E | SEG_D ,                           // L
  SEG_E | SEG_F | SEG_A | SEG_B | SEG_C | SEG_G ,   // A
  0x00 ,
};

uint8_t PomVypis[] = { 0x00, 0x00, 0x00, 0x00 };

//Hodnoty pro formátování displeje
long BlikaniMil;
bool StavBlikani = true;
long OdpocetMil;
bool OdpocetStav = true;

// funkce pro vypnutí vnitřních hodin
ISR (WDT_vect)
{
  wdt_disable();
}

void setup() {
  // nastavení pinů jako výstupních
  pinMode(DIR_MIN, OUTPUT);
  pinMode(STEP_MIN, OUTPUT);
  pinMode(DIR_HOD, OUTPUT);
  pinMode(STEP_HOD, OUTPUT);
  pinMode(SLP_HOD, OUTPUT);
  pinMode(SLP_MIN, OUTPUT);
  pinMode(BUZZER, OUTPUT);

  // připojení obou řídících pinů na zem
  digitalWrite(DIR_HOD, LOW);
  digitalWrite(STEP_HOD, LOW);
  digitalWrite(DIR_MIN, LOW);
  digitalWrite(STEP_MIN, LOW);

  digitalWrite(SLP_HOD, LOW);
  digitalWrite(SLP_MIN, LOW);

  // nastavení pinů jako vstupních
  pinMode(SET_TIME, INPUT_PULLUP);
  pinMode(UP_TIME, INPUT_PULLUP);
  pinMode(DOWN_TIME, INPUT_PULLUP);
  pinMode(KON_HOD, INPUT_PULLUP);
  pinMode(KON_MIN, INPUT_PULLUP);

  RTC.setClockMode(false); //nastavení 24 hodinového formátu času

  //funkce pro hardwarové přerušení právě probíhajícího programu
  //na základě stisknutí tlačítka SET
  attachInterrupt(digitalPinToInterrupt(SET_TIME), Vzbudit, RISING);

  //Nastavení výchozí polohy
  HomeHod();
  HomeMin();
}

void loop() {
  Mode(); //kontrola stisku tlačítka SET

  Debounce (); //funkce pro odstrnění zákmitů u tlačítek

  if (SetTimeMode == 0)
  {
    Synchronizace(); //funkce pro synchronizaci aktuálního času a polohy ciferníků
    Alarm(); //funkce pro ověření spuštění alarmu

    if (Hodiny == HodinyPol && Minuty == MinutyPol && AlarmStav == false)
    {
      enStiskSetTime == 1;
      Uspat(); //přechod do režimu s nízkým odběrem proudu
    }
  }

  else
  {
    NastaveniCasu(); //funkce pro nastavení času a alarmu
  }

}

//ošetření zákmitu tlačítek
//pokud je stisk tlačítka zakázaný tak ho povol po uplynutí 200 milisekund
void Debounce () {
  if (enStiskSetTime == 0) {
    if (millis() - stiskMilSetTime > 200) {
      enStiskSetTime = 1;
    }
  }

  if (enStiskUpTime == 0) {
    if (millis() - stiskMilUpTime > 200) {
      enStiskUpTime = 1;
    }
  }

  if (enStiskDownTime == 0) {
    if (millis() - stiskMilDownTime > 200) {
      enStiskDownTime = 1;
    }
  }
}

//stisk tlačítka SET
//nastavení prostředního tlačítka
// pokud je zvuková signalizace aktivní vypni ji, pokud ne nastav aktuální čas hodin
void Mode() {
  stavTlacSetTime = digitalRead(SET_TIME);
  if (stavTlacSetTime == LOW & enStiskSetTime == 1)
  {
    if (AlarmStav == true)
    {
      AlarmStav = false;
      AlarmOvladani = false;
    }

    else
    {
      SetTimeMode = SetTimeMode + 1;
      OdpocetMil = millis();
    }

    stiskSetTime = HIGH;
  }
  if (stiskSetTime == HIGH) {
    stiskMilSetTime = millis();
    enStiskSetTime = 0;
    stiskSetTime = LOW;
  }
}

//funkce pro nastavení aktuálního času
void NastaveniCasu() {
  //Načtení potřebných hodnot
  if (SetTimeMode == 1)
  {
    Hodiny = RTC.getHour(h12, PM);
    Minuty = RTC.getMinute();
    display.setBrightness(7, true);
    //display.setBrightness(0x0f);
    display.clear();
    display.setSegments(SEG_SET);
    delay(1000);
    SetTimeMode = 2;
  }
  //Nastavení hodin
  if (SetTimeMode == 2)
  {
    Blikani();
    UpHodiny();
    DownHodiny();
    Odpocet();
  }
  //Nastavení minut
  if (SetTimeMode == 3)
  {
    Blikani();
    UpMinuty();
    DownMinuty();
    Odpocet();
  }
  //Uložení hodnot do RTC modulu
  if (SetTimeMode == 4)
  {
    RTC.setHour(Hodiny);
    RTC.setMinute(Minuty);
    RTC.setClockMode(false);
    display.showNumberDecEx(RTC.getHour(h12, PM), 0b01000000, true, 2, 0);
    display.showNumberDecEx(RTC.getMinute(), 0b01000000, true, 2, 2);
    delay(1000);
    display.clear();
    display.setSegments(SEG_ALARM);
    Hodiny = HodinyAlarm;
    Minuty = MinutyAlarm;
    delay(1000);
    SetTimeMode = 5;
  }
  //Nastavení alarmu - hodiny
  if (SetTimeMode == 5)
  {
    Blikani();
    UpHodiny();
    DownHodiny();
    Odpocet();
  }
  //Nastavení alarmu - minuty
  if (SetTimeMode == 6)
  {
    Blikani();
    UpMinuty();
    DownMinuty();
    Odpocet();
  }
  //Nastavení alarmu - zapnutí
  if (SetTimeMode == 7)
  {
    if (AlarmOvladani == false)
    {
      display.setSegments(SEG_OFF);
    }
    if (AlarmOvladani == true)
    {
      display.setSegments(SEG_ON);
    }
    ToggleOnOff();
    Odpocet();
  }
  //Uložení nastavení alarmu
  if (SetTimeMode == 8)
  {
    HodinyAlarm = Hodiny;
    MinutyAlarm = Minuty;
    display.showNumberDecEx(HodinyAlarm, 0b01000000, true, 2, 0);
    display.showNumberDecEx(MinutyAlarm, 0b01000000, true, 2, 2);
    delay(2000);
    display.clear();
    SetTimeMode = 0;
  }
}

//zvyšuje nastavení hodinové hodnoty
void UpHodiny() {
  stavTlacUpTime = digitalRead(UP_TIME);
  if (stavTlacUpTime == LOW & enStiskUpTime == 1)
  {
    Hodiny = Hodiny + 1;
    if (Hodiny > 23)
    {
      Hodiny = 0;
    }
    OdpocetMil = millis();
    stiskUpTime = HIGH;
  }
  if (stiskUpTime == HIGH) {
    stiskMilUpTime = millis();
    enStiskUpTime = 0;
    stiskUpTime = LOW;
  }
}

//snižuje nastavení hodinové hodnoty
void DownHodiny() {
  stavTlacDownTime = digitalRead(DOWN_TIME);
  if (stavTlacDownTime == LOW & enStiskDownTime == 1)
  {
    Hodiny = Hodiny - 1;
    if (Hodiny < 0)
    {
      Hodiny = 23;
    }
    OdpocetMil = millis();
    stiskDownTime = HIGH;
  }
  if (stiskDownTime == HIGH) {
    stiskMilDownTime = millis();
    enStiskDownTime = 0;
    stiskDownTime = LOW;
  }
}

//zvyšuje nastavení minutové hodnoty
void UpMinuty() {
  stavTlacUpTime = digitalRead(UP_TIME);
  if (stavTlacUpTime == LOW & enStiskUpTime == 1)
  {
    Minuty = Minuty + 1;
    if (Minuty > 59)
    {
      Minuty = 0;
    }
    OdpocetMil = millis();
    stiskUpTime = HIGH;
  }
  if (stiskUpTime == HIGH) {
    stiskMilUpTime = millis();
    enStiskUpTime = 0;
    stiskUpTime = LOW;
  }
}

//snižuje nastavení minutové hodnoty
void DownMinuty() {
  stavTlacDownTime = digitalRead(DOWN_TIME);
  if (stavTlacDownTime == LOW & enStiskDownTime == 1)
  {
    Minuty = Minuty - 1;
    if (Minuty < 0)
    {
      Minuty = 59;
    }
    OdpocetMil = millis();
    stiskDownTime = HIGH;
  }
  if (stiskDownTime == HIGH) {
    stiskMilDownTime = millis();
    enStiskDownTime = 0;
    stiskDownTime = LOW;
  }
}

//přepíná mezi zapnutím a vypnutím alarmu
void ToggleOnOff() {
  stavTlacDownTime = digitalRead(DOWN_TIME);
  if (stavTlacDownTime == LOW & enStiskDownTime == 1)
  {
    display.clear();
    AlarmOvladani = !AlarmOvladani;
    OdpocetMil = millis();
    stiskDownTime = HIGH;
  }
  if (stiskDownTime == HIGH) {
    stiskMilDownTime = millis();
    enStiskDownTime = 0;
    stiskDownTime = LOW;
  }

  stavTlacUpTime = digitalRead(UP_TIME);
  if (stavTlacUpTime == LOW & enStiskUpTime == 1)
  {
    display.clear();
    AlarmOvladani = !AlarmOvladani;
    OdpocetMil = millis();
    stiskUpTime = HIGH;
  }
  if (stiskUpTime == HIGH) {
    stiskMilUpTime = millis();
    enStiskUpTime = 0;
    stiskUpTime = LOW;
  }
}

//nastavení výchozí polohy hodinového ciferníku
void HomeHod() {
  digitalWrite(DIR_HOD, LOW);
  digitalWrite(SLP_HOD, HIGH);

  while (1)
  {
    stavTlacKonHod = digitalRead(KON_HOD);

    if (stavTlacKonHod == LOW)
    {
      HodinyPol = 0;
      digitalWrite(SLP_HOD, LOW);
      break;
    }
    digitalWrite(STEP_HOD, HIGH);
    delayMicroseconds(Rychlost);
    digitalWrite(STEP_HOD, LOW);
    delayMicroseconds(Rychlost);
  }
}

//nastavení výchozí polohy minutového ciferníku
void HomeMin() {
  digitalWrite(DIR_MIN, HIGH);
  digitalWrite(SLP_MIN, HIGH);

  while (1)
  {
    stavTlacKonMin = digitalRead(KON_MIN);

    if (stavTlacKonMin == LOW)
    {
      MinutyPol = 0;
      digitalWrite(SLP_MIN, LOW);
      break;
    }

    digitalWrite(STEP_MIN, HIGH);
    delayMicroseconds(Rychlost);
    digitalWrite(STEP_MIN, LOW);
    delayMicroseconds(Rychlost);
  }
}

//zajišťuje synchronizaci aktuálního a zobrazovaného času
void Synchronizace() {
  Hodiny = RTC.getHour(h12, PM);
  Minuty = RTC.getMinute();

  if (Hodiny > 12)
  {
    Hodiny = RTC.getHour(h12, PM) - 12;
  }

  if (Hodiny > HodinyPol)
  {
    digitalWrite(DIR_HOD, HIGH);
    digitalWrite(SLP_HOD, HIGH);
    delay(1);
    while (Hodiny > HodinyPol)
    {
      HodPosun();
    }
    digitalWrite(SLP_HOD, LOW);
  }

  if (Minuty > MinutyPol)
  {
    digitalWrite(DIR_MIN, LOW);
    digitalWrite(SLP_MIN, HIGH);
    delay(1);
    while (Minuty > MinutyPol)
    {
      MinPosun();
    }
    digitalWrite(SLP_MIN, LOW);
  }

  if (Hodiny < HodinyPol)
  {
    HomeHod();
  }

  if (Minuty < MinutyPol)
  {
    HomeMin();
  }
}

//posun o 1 minutu
void MinPosun() {
  for (int i = 0; i <= KrokyMin; i++)
  {
    digitalWrite(STEP_MIN, HIGH);
    delayMicroseconds(Rychlost);
    digitalWrite(STEP_MIN, LOW);
    delayMicroseconds(Rychlost);
  }
  MinutyPol = MinutyPol + 1;
}

//posun o 1 hodinu
void HodPosun() {
  for (int i = 0; i <= KrokyHod; i++)
  {
    digitalWrite(STEP_HOD, HIGH);
    delayMicroseconds(Rychlost);
    digitalWrite(STEP_HOD, LOW);
    delayMicroseconds(Rychlost);
  }
  HodinyPol = HodinyPol + 1;
}

//Mód šetření energií
void Uspat() {
  digitalWrite(DIR_HOD, LOW);
  digitalWrite(STEP_HOD, LOW);
  digitalWrite(DIR_MIN, LOW);
  digitalWrite(STEP_MIN, LOW);
  digitalWrite(SLP_HOD, LOW);
  digitalWrite(SLP_MIN, LOW);
  display.clear();
  // vypne ADC
  ADCSRA = 0;
  // clear various "reset" flags
  MCUSR = 0;
  // allow changes, disable reset
  WDTCSR = bit (WDCE) | bit (WDE);
  // Nastavení přerušení a časový interval
  WDTCSR = bit (WDIE) | bit (WDP3) | bit (WDP0);    // nastav WDIE, a 8 sekundový delay
  wdt_reset();
  set_sleep_mode (SLEEP_MODE_PWR_DOWN);
  noInterrupts ();
  sleep_enable();
  attachInterrupt (0, Vzbudit, FALLING);
  EIFR = bit (INTF0);
  MCUCR = bit (BODS) | bit (BODSE);
  MCUCR = bit (BODS);
  interrupts ();
  sleep_cpu ();

  sleep_disable();
}

// vypnout mód pro šetření energií
void Vzbudit()
{
  sleep_disable();
  detachInterrupt (0);
}

//podprogram zajišťující problikávání právně nastavované hodnoty na displeji
void Blikani() {
  if (StavBlikani)
  {
    BlikaniMil = millis();
    StavBlikani = false;
  }

  if ((millis() - BlikaniMil) < 500)
  {
    if (SetTimeMode == 2 || SetTimeMode == 5)
    {
      PomVypis[0] = 0x00;
      PomVypis[1] = 0x00;
      PomVypis[2] = display.encodeDigit(Minuty / 10);
      PomVypis[3] = display.encodeDigit(Minuty % 10);
      display.setSegments(PomVypis);
    }
    if (SetTimeMode == 3 || SetTimeMode == 6)
    {
      PomVypis[0] = display.encodeDigit(Hodiny / 10);
      PomVypis[1] = display.encodeDigit(Hodiny % 10);
      PomVypis[2] = 0x00;
      PomVypis[3] = 0x00;
      display.setSegments(PomVypis);
    }
  }
  if ((millis() - BlikaniMil) > 500)
  {
    display.showNumberDecEx(Hodiny, 0b01000000, true, 2, 0);
    display.showNumberDecEx(Minuty, 0b01000000, true, 2, 2);

    if ((millis() - BlikaniMil) > 1000)
    {
      StavBlikani = true;
    }
  }
}

//vypne režim pro nastavení aktuálního času při absenci vstupu, která trvá déle než jednu minutu
void Odpocet() {
  if ((millis() - OdpocetMil) > 60000)
  {
    if (SetTimeMode < 4)
    {
      RTC.setHour(Hodiny);
      RTC.setMinute(Minuty);
      RTC.setClockMode(false);
      Hodiny = RTC.getHour(h12, PM);
      Minuty = RTC.getMinute();
      display.showNumberDecEx(Hodiny, 0b01000000, true, 2, 0);
      display.showNumberDecEx(Minuty, 0b01000000, true, 2, 2);
      delay(1000);
      display.clear();
      SetTimeMode = 0;
    }
    else
    {
      SetTimeMode = 8;
    }
  }
}

//funkce alarmu
//pokud je alarm aktivní srovnej aktuální a nastavený čas pro alarm, pokud jsou shodné  zapni zvukovou signalizaci
void Alarm() {
  if (RTC.getHour(h12, PM) == HodinyAlarm && RTC.getMinute() == MinutyAlarm && AlarmOvladani == true)
  {
    AlarmStav = true;
  }

  if (AlarmStav == true)
  {
    for (int i = 0; i <= 3; i++)
    {
      tone(BUZZER, 500);
      delay(50);
      noTone(BUZZER);
      delay(50);
    }
    delay(1000);
  }
}
